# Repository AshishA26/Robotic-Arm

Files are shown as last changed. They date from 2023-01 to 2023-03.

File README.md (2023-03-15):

# Robotic-Arm
A robotic arm that mimics a user's arm gestures. It is purposed to help people with disabilities and meant for remote operations, and can also be used as a prototype in various other cases.

There are 2 parts to this project. The 1st part is the robotic arm itself, which has 5 DOF (5 servos / 5 "Degrees of Freedom") and uses an Arduino Nano, a Dedicated Servo Driver, and an NRF24L01 for recieving signals. The 2nd part is a gesture controller that straps onto the user's body. It has an Arduino Nano, an NRF24L01 module for transmitting data to the robotic arm, and 2 MPU6050's. The MPU6050s are velcroed onto the user's wrists, and then each direction of motion the user moves an arm in, causes a servo to move.

Programmed in `Arduino IDE`, models created in `Solidworks`, schematics created in `KiCad`.

Here is a very quick demo of the robotic arm being manipulated by the gesture controller that is strapped onto me. The full video is available [here](https://www.youtube.com/watch?v=RmKj0so72yQ). (Note: The white object in my hand is a switch to remotely power on/off the robotic arm.)
Link to youtube video (https://www.youtube.com/watch?v=RmKj0so72yQ)

Additionally, I made a demo video showing all the joints in the robotic arm moving one by one (using the gesture controller), which is available for viewing [here](https://www.youtube.com/watch?v=eJz9jL7be58).

A picture of the Robotic Arm:
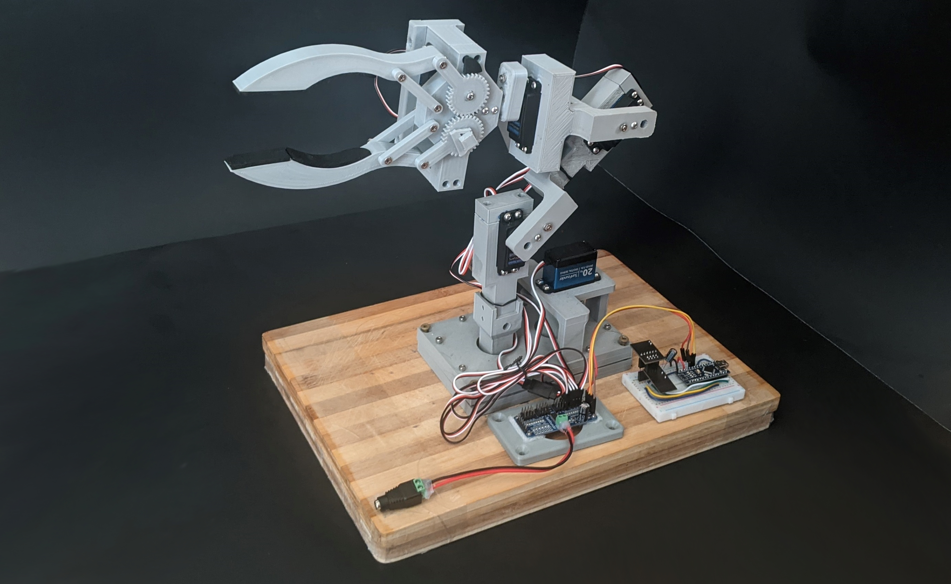
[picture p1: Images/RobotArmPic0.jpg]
RobotArmPic5


A picture of the Gesture Controller:
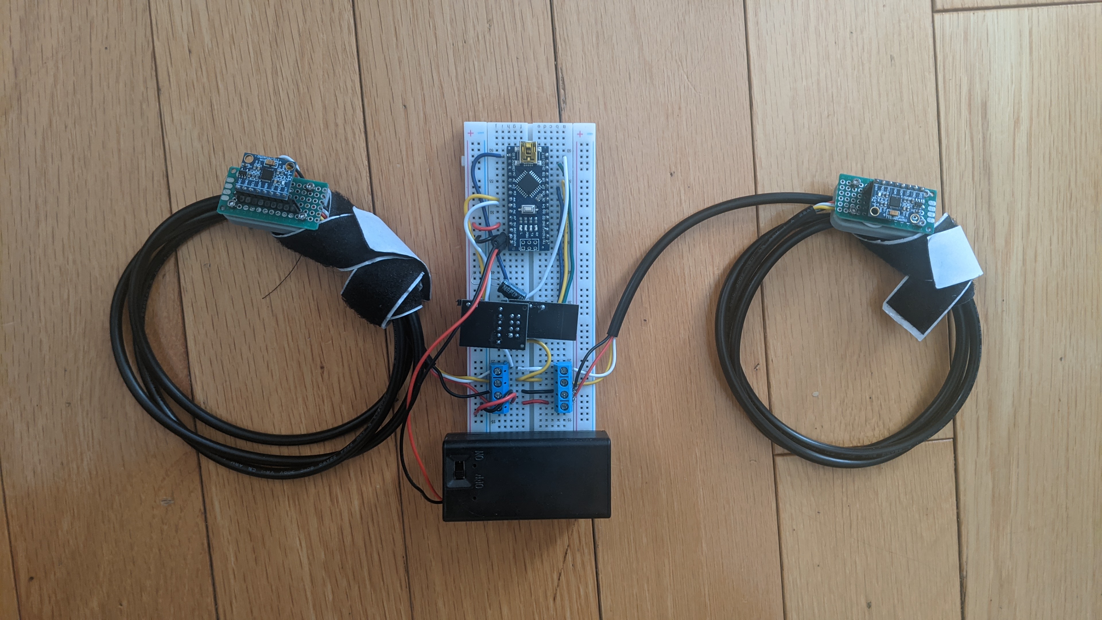
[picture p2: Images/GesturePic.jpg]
RobotArmPic6


## Schematics
RobotArmSchematic

## Demos
Some demos showing how certain mechanisms in the robotic arm work.

| Gear Movement Demo | Backside of Gears |
| :---: | :---: |
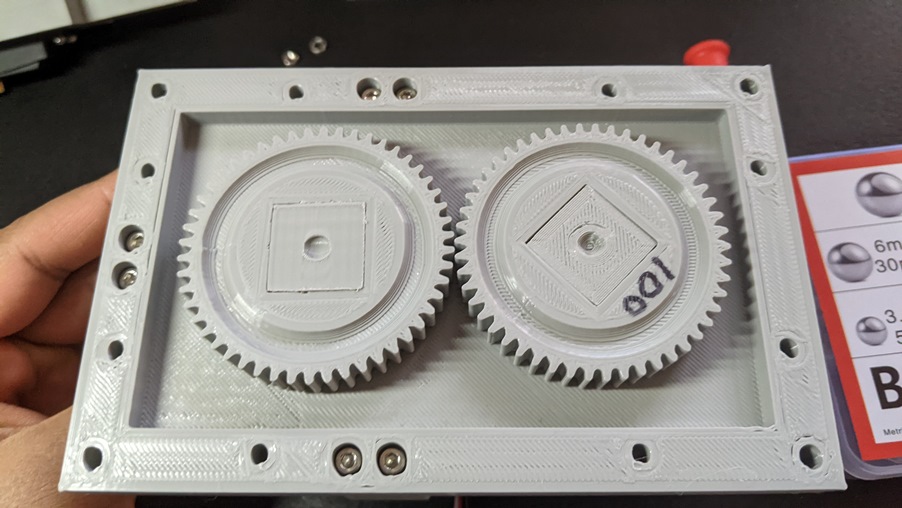
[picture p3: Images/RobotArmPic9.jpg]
BacksideOfGears
| GearDemo  |  |

<p align="center">
    <strong>Claw Demo</strong>
</p>

<p align="center">
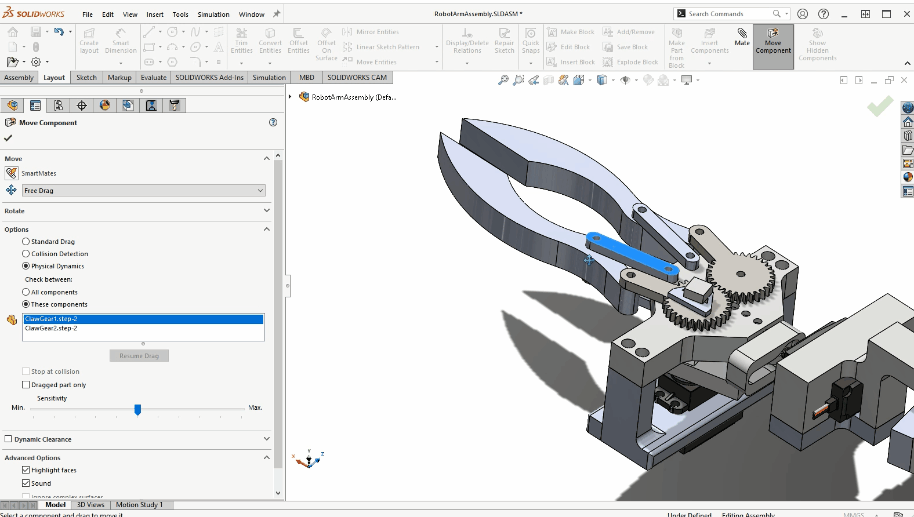
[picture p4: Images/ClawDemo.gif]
  
</p>

## Other Images
Rendered pictures of the 3D model I created using my own models designed for 3D printing combined with the servos from [GrabCAD](https://grabcad.com/library). Made in real-world scale and was designed using Solidworks:
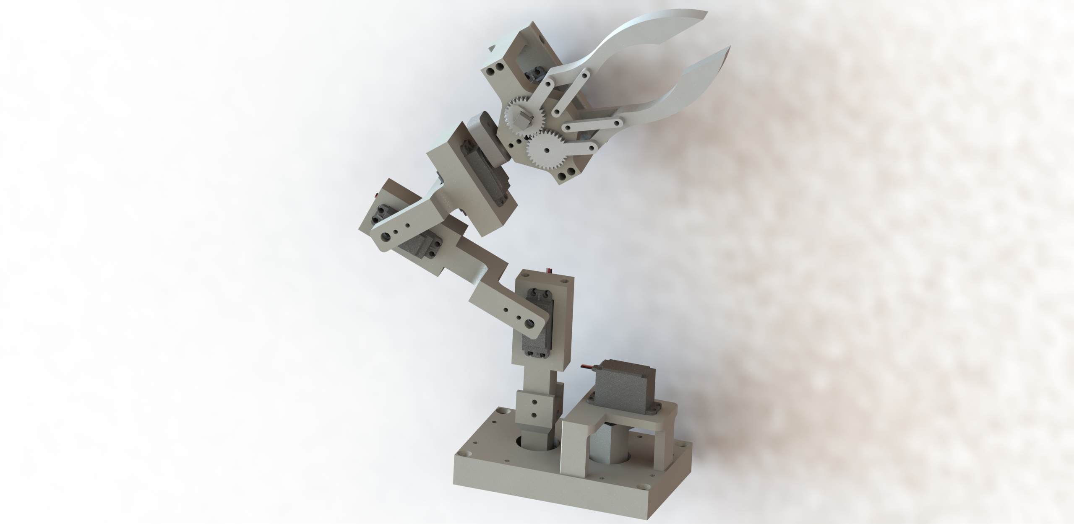
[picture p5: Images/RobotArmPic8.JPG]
RobotArmPic5


Render of gear mechanism underneath the lid.
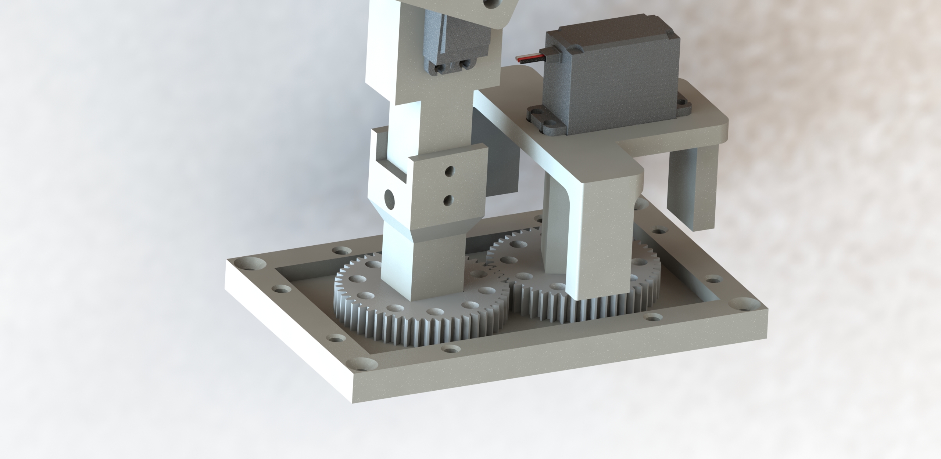
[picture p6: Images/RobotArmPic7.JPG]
RobotArmPic5


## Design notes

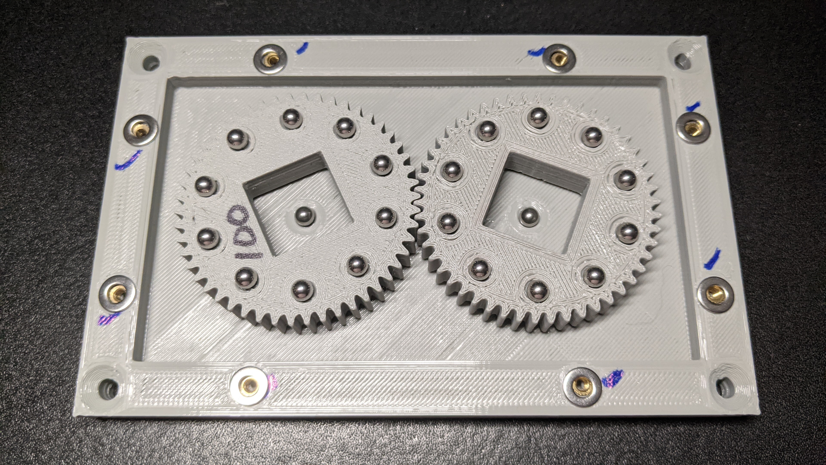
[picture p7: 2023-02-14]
Images/RobotArmPic10.jpg

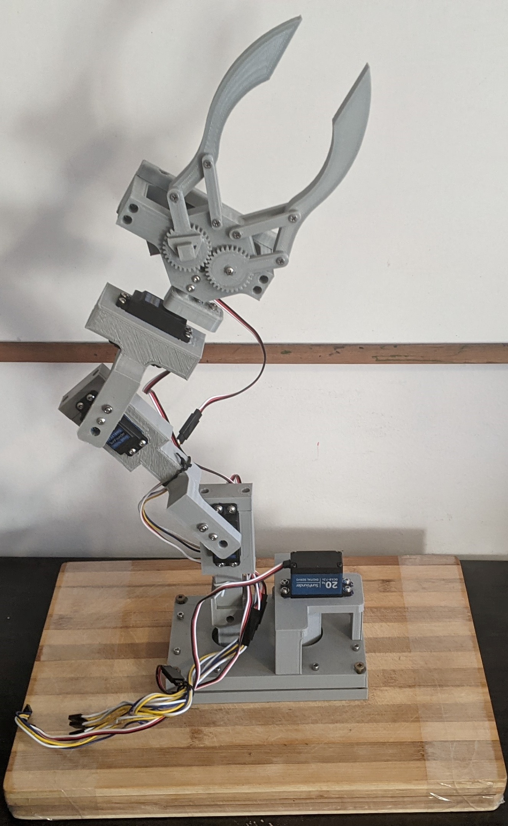
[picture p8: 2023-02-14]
Images/RobotArmPic6Cropped.jpg

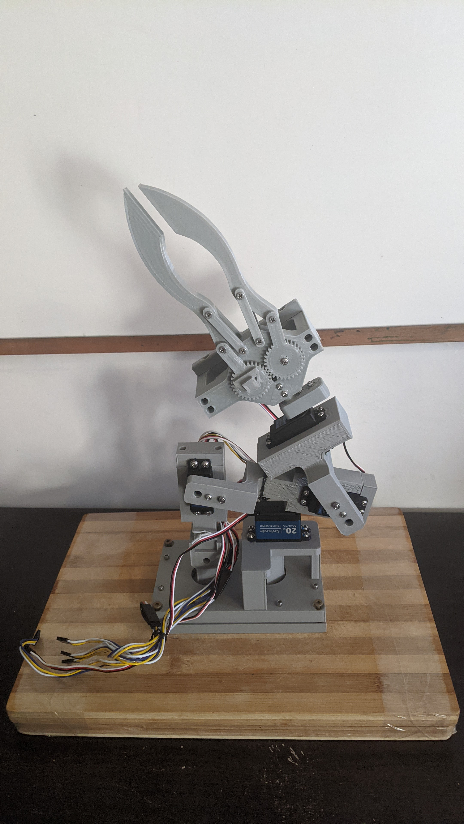
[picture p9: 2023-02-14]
Images/RobotArmPic2.jpg

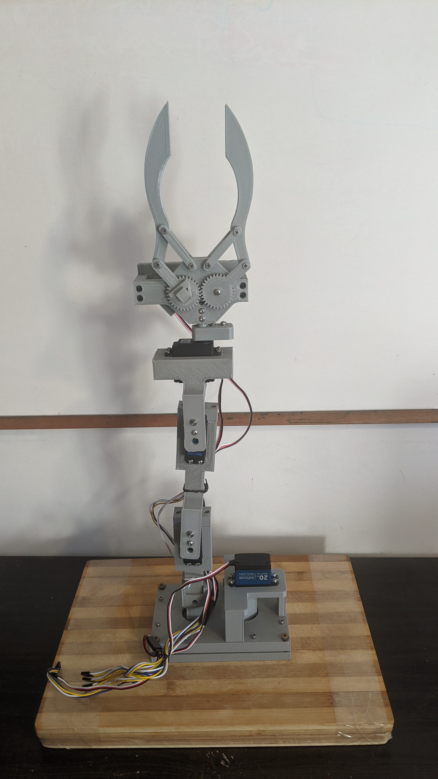
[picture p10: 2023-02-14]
Images/RobotArmPic1.jpg

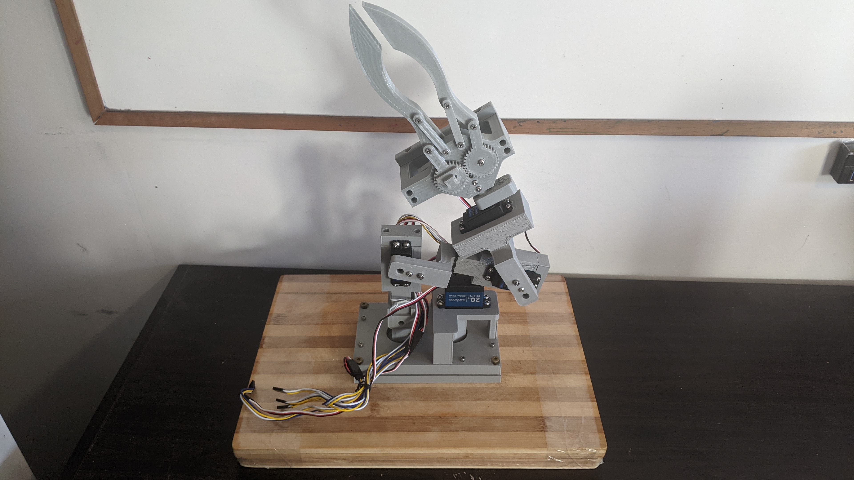
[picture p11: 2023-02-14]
Images/RobotArmPic4.jpg

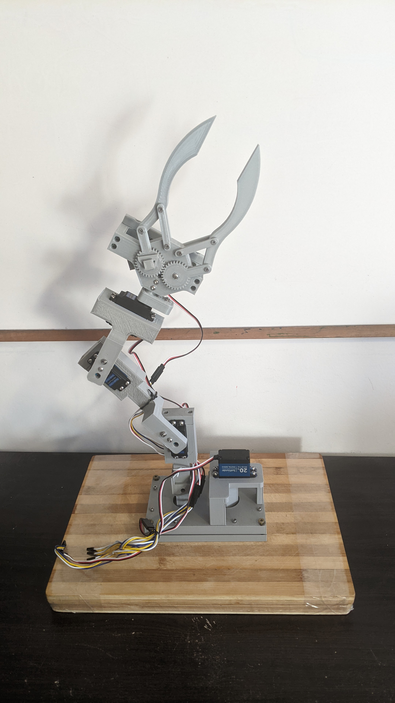
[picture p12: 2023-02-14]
Images/RobotArmPic3.jpg

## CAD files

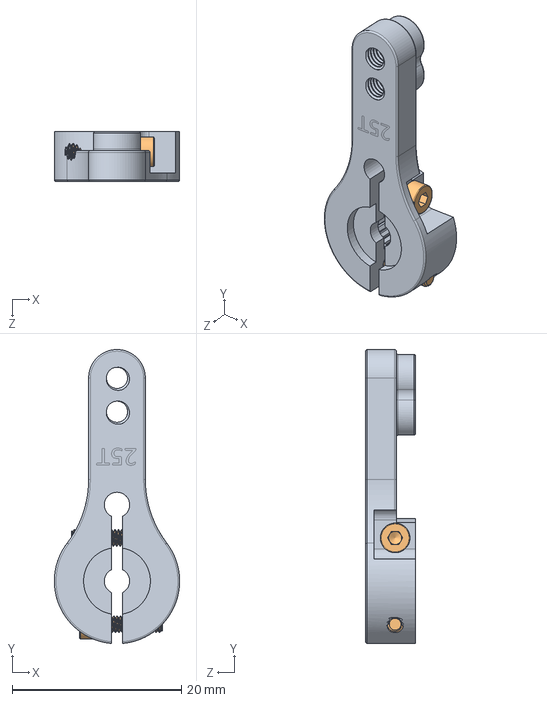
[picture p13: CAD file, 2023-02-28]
Models/Assembly/SERVO ARM HORN 25T ALUMINIUM/SERVO ARM HORN WITH FASTENERS.SLDASM
14.8 x 34.7 x 5.90 mm
SERVO ARM HORN 25T ALUMINIUM
M2 CAP HEAD SOCKET SCREW x 2

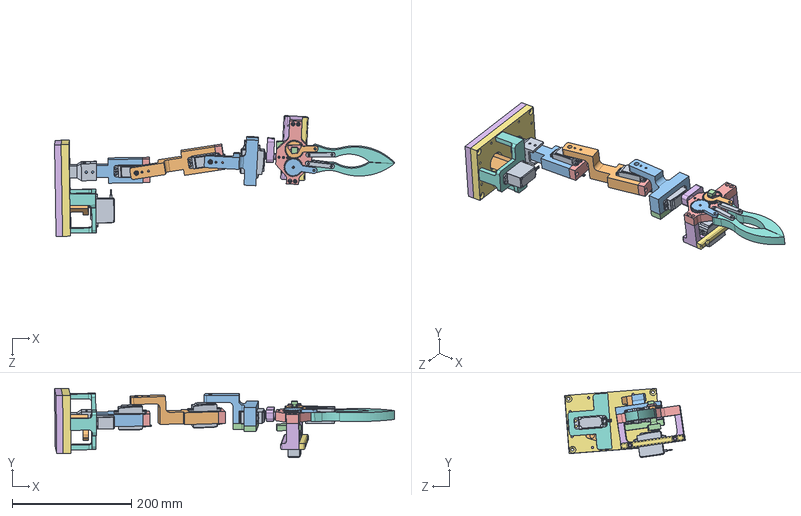
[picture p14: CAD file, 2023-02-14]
Models/Assembly/RobotArmAssembly.SLDASM
569.9 x 115.9 x 202.6 mm
sunfounder_20kgSLDPRT x 5
ServoArmMount
ArmPt1
ShaftGearSTEP x 2
ArmPt1Top x 2
BottomSideBaseCase
TopSideBaseCase
BaseServoStand
ArmExtension
ArmPt2
ArmPt3
ArmPt3Top
ArmPt4
ArmPt4ServoHolder
ArmPt4ServoHolderScrew
ClawGripper x 2
ClawJoint x 4
ClawGear1.step
ClawGear2.step
ServotoGear
ServotoGearClip
ArmPt4ServoArm

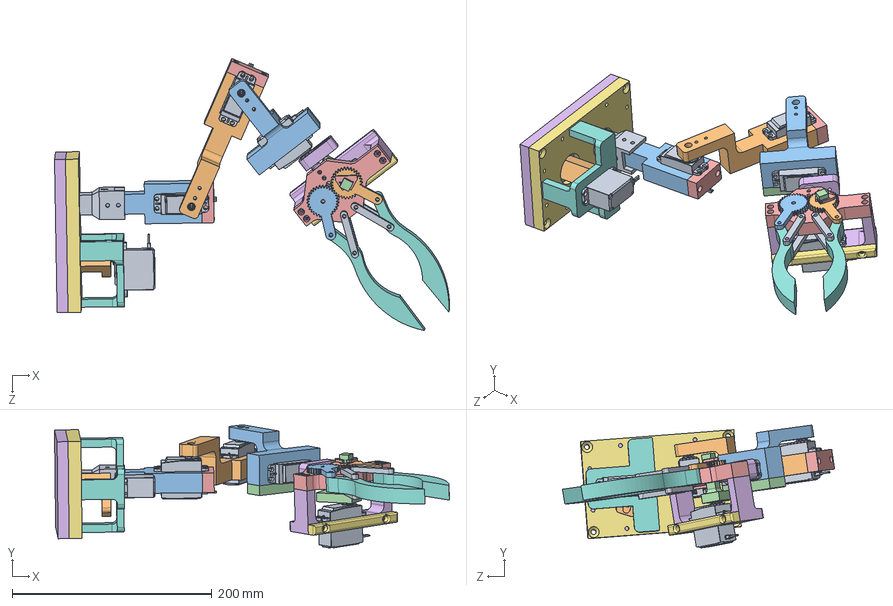
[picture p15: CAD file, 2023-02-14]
Models/Assembly/RobotArmAssemblyInBentShape.SLDASM
396.0 x 123.3 x 272.9 mm
sunfounder_20kgSLDPRT x 5
ServoArmMount
ArmPt1
ShaftGearSTEP x 2
ArmPt1Top x 2
BottomSideBaseCase
TopSideBaseCase
BaseServoStand
ArmExtension
ArmPt2
ArmPt3
ArmPt3Top
ArmPt4
ArmPt4ServoHolder
ArmPt4ServoHolderScrew
ClawGripper x 2
ClawJoint x 4
ClawGear1.step
ClawGear2.step
ServotoGear
ServotoGearClip
ArmPt4ServoArm

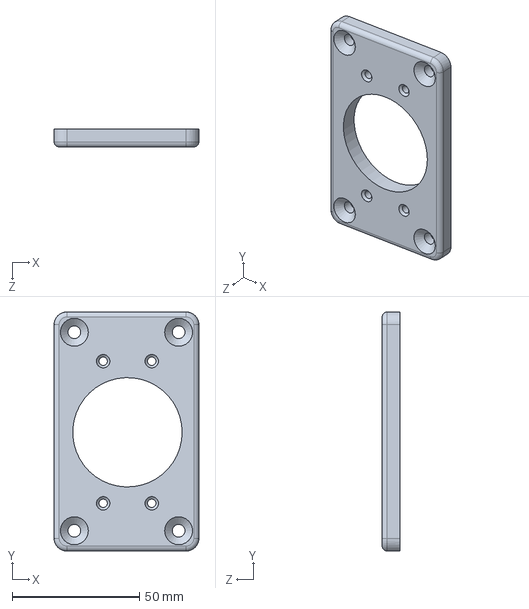
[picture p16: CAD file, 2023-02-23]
Models/Assembly/ServoDriverHolder.SLDPRT
57.0 x 94.0 x 7.00 mm

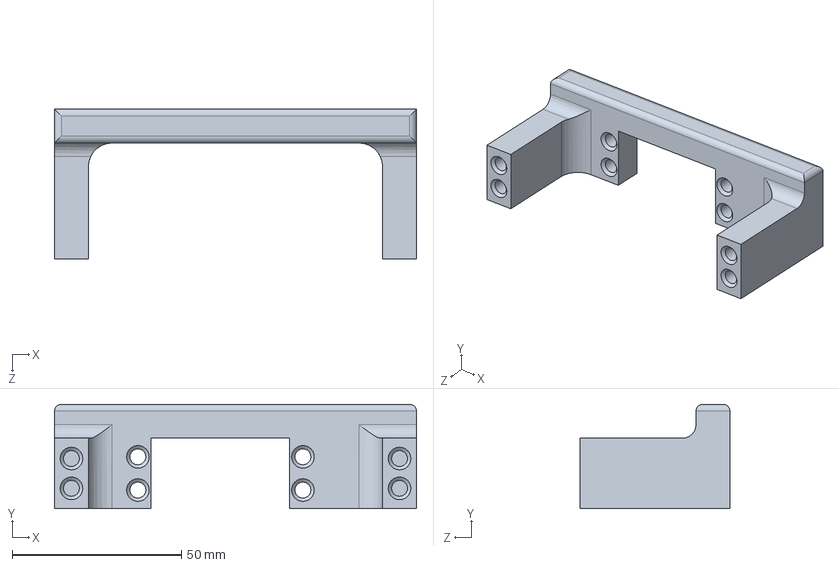
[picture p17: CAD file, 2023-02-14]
Models/Assembly/ArmPt4ServoHolder.SLDPRT
106.8 x 30.8 x 44.2 mm

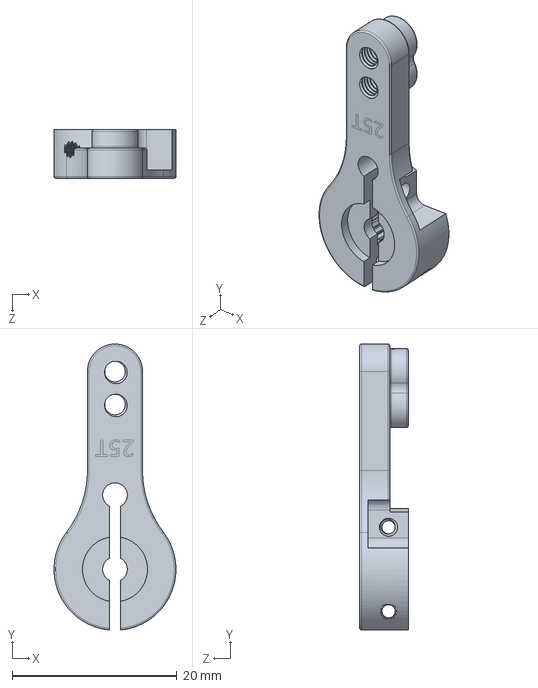
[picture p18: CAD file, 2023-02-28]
Models/Assembly/SERVO ARM HORN 25T ALUMINIUM/SERVO ARM HORN 25T ALUMINIUM.SLDPRT
14.8 x 34.7 x 5.90 mm

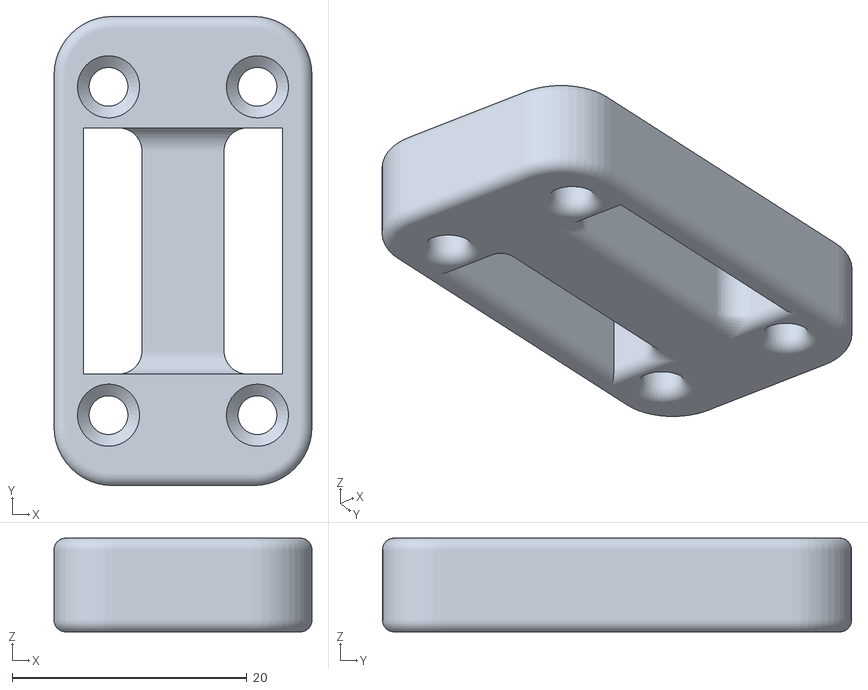
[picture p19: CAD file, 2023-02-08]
Models/STL/WristbandV1.STL
22.0 x 40.0 x 8.00

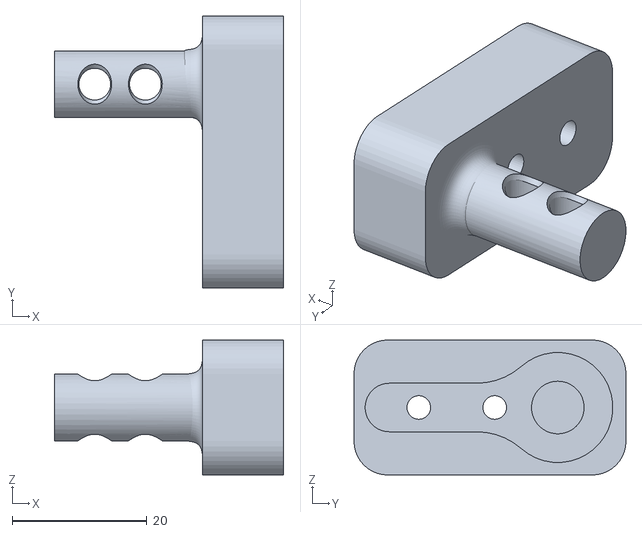
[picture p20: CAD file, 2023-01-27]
Models/STL/ArmPt4ServoArm.STL
34.0 x 40.3 x 20.0

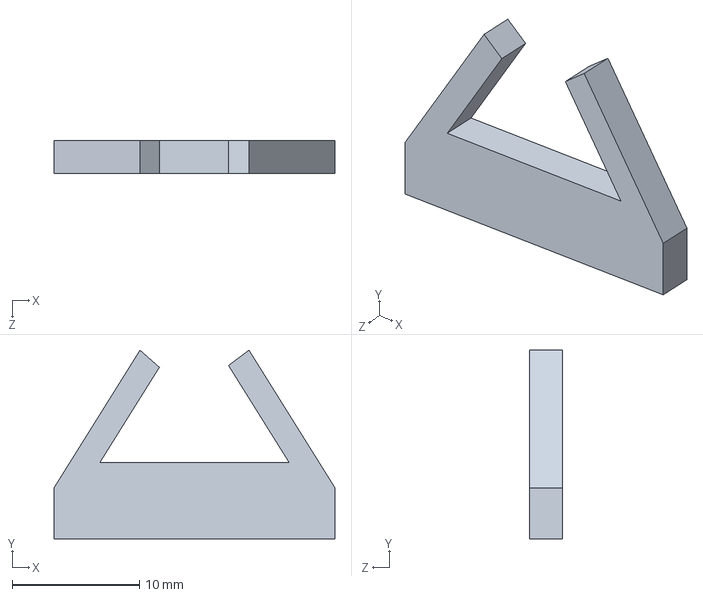
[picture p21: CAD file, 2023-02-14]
Models/Assembly/ServotoGearClip.SLDPRT
22.0 x 14.8 x 2.60 mm

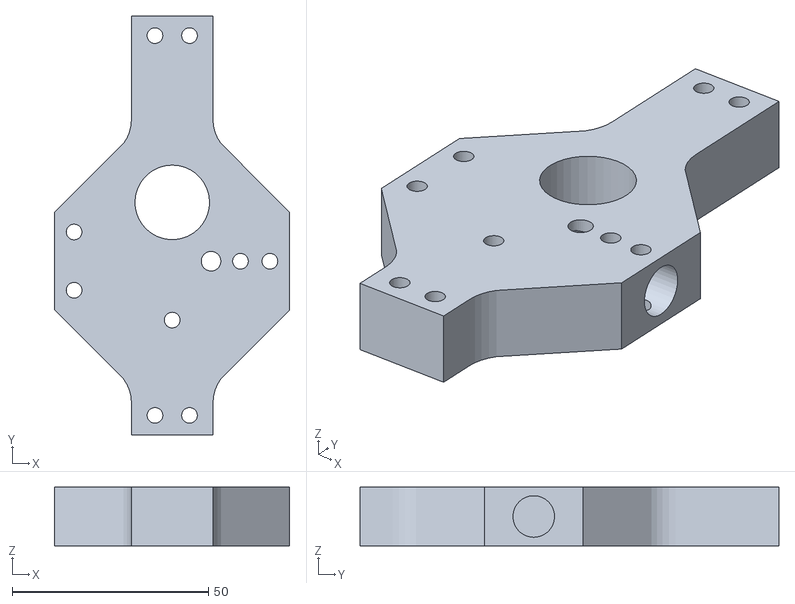
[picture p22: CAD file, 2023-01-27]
Models/STL/ArmPt4.STL
59.9 x 106.8 x 15.0

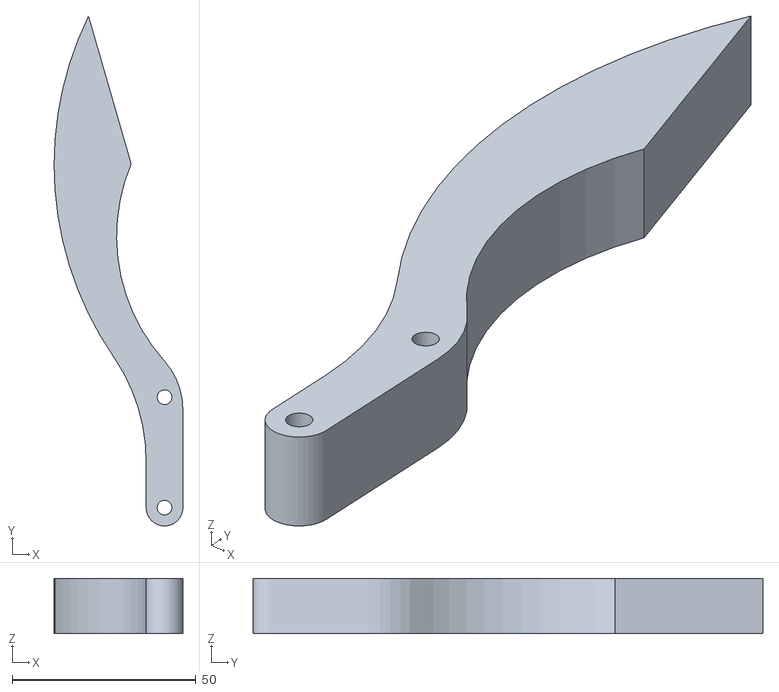
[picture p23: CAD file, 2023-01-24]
Models/STL/ClawGripper.STL
35.0 x 138.6 x 15.0

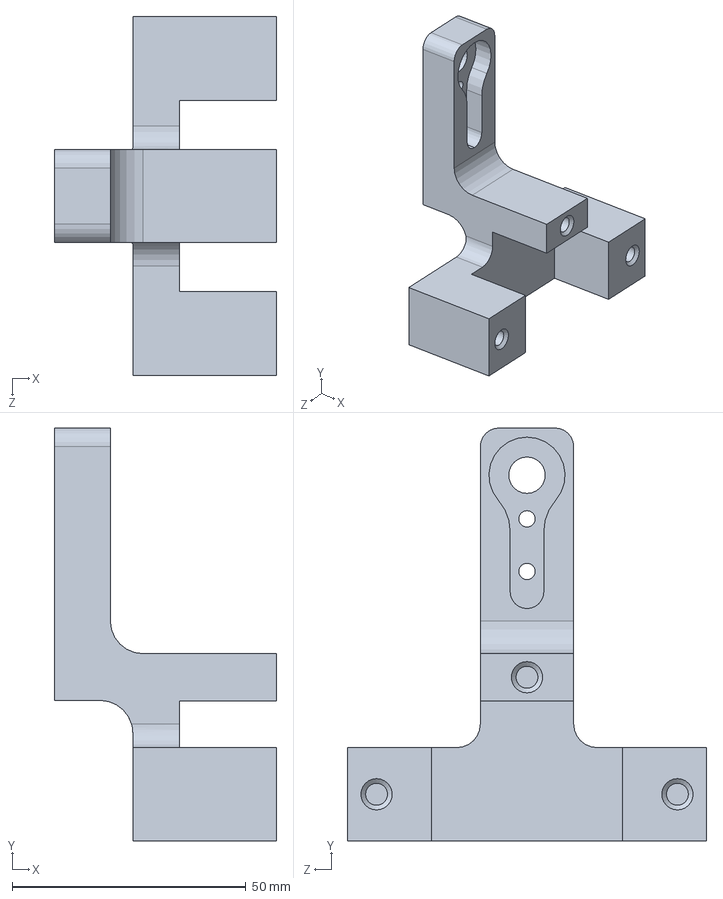
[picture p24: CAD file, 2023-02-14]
Models/Assembly/ArmPt3.SLDPRT
47.6 x 88.4 x 76.9 mm

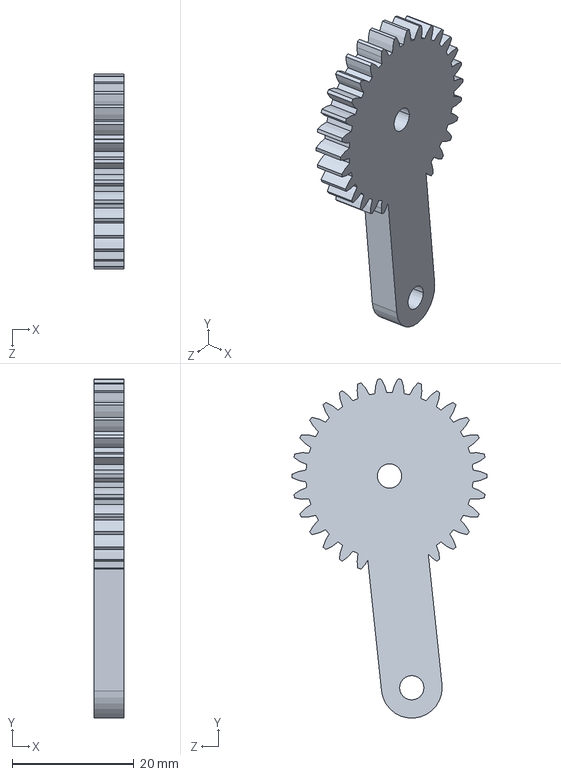
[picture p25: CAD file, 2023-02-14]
Models/Assembly/ClawGear2.step.SLDPRT
5.00 x 55.7 x 32.0 mm

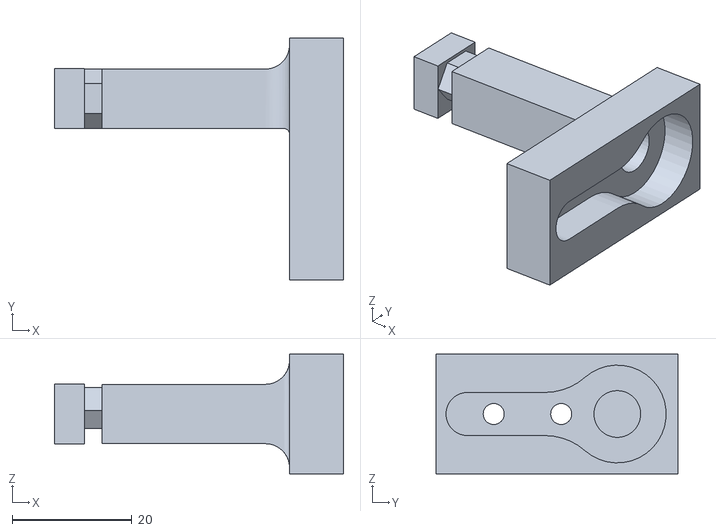
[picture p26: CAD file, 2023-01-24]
Models/STL/ServotoGear.STL
48.2 x 40.3 x 20.0

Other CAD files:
Models/STL/ServoDriverHolder.STL
Models/STL/ArmPt4ServoHolder.STL
Models/STL/ClawJoint.STL
Models/Assembly/ShaftGearSTEP.SLDPRT
Models/Assembly/ArmExtension.SLDPRT
Models/Assembly/ArmPt1.SLDPRT
Models/Assembly/ArmPt1Top.SLDPRT
Models/Assembly/ArmPt2.SLDPRT
Models/Assembly/ArmPt3Top.SLDPRT
Models/Assembly/ArmPt4.SLDPRT
Models/Assembly/ArmPt4ServoArm.SLDPRT
Models/Assembly/ArmPt4ServoHolderScrew.SLDPRT
Models/Assembly/BaseServoStand.SLDPRT
Models/Assembly/BottomSideBaseCase.SLDPRT
Models/Assembly/ClawGear1.SLDPRT
Models/Assembly/ClawGear1.step.SLDPRT
Models/Assembly/ClawGear2.SLDPRT
Models/Assembly/ClawGripper.SLDPRT
Models/Assembly/ClawJoint.SLDPRT
Models/Assembly/SERVO ARM HORN 25T ALUMINIUM/M2 CAP HEAD SOCKET SCREW.SLDPRT
Models/Assembly/SERVO ARM HORN 25T ALUMINIUM/M2 x 8 CAP HEAD SOCKET SCREW.IGS
Models/Assembly/SERVO ARM HORN 25T ALUMINIUM/M2 x 8 CAP HEAD SOCKET SCREW.STEP
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

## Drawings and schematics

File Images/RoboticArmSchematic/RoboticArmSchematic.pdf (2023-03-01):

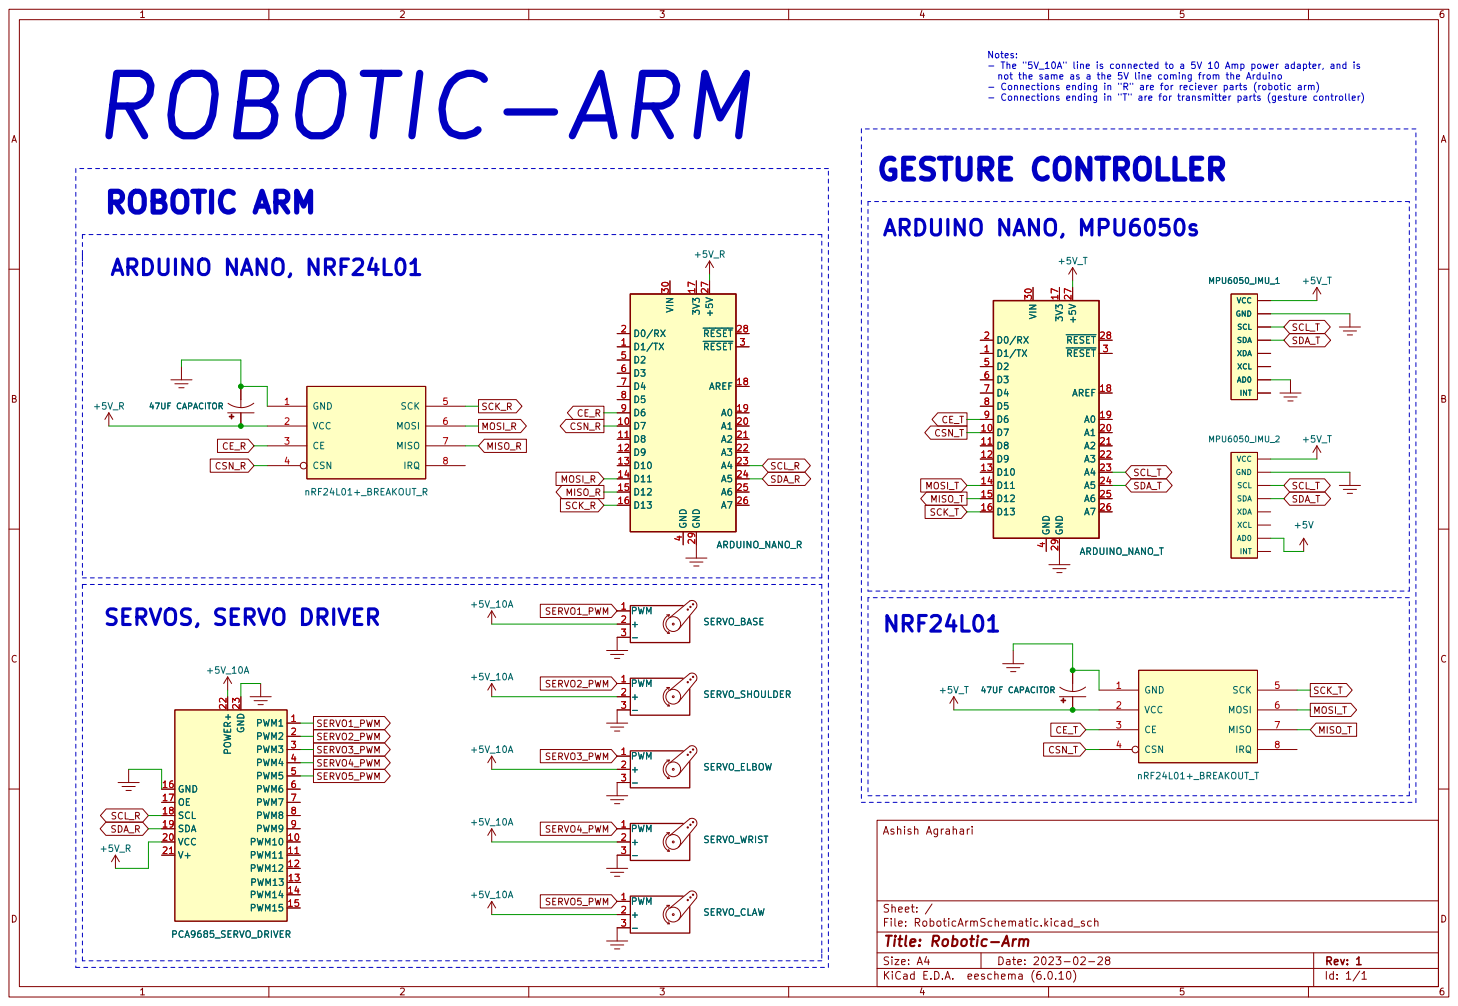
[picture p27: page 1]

Notes: - The "5V_10A" line is connected to a 5V 10 Amp power adapter, and is
~{RESET}28 GND 29

not the same as a the 5V line coming from the Arduino
- Connections ending in "R" are for reciever parts (robotic arm)
- Connections ending in "T" are for transmitter parts (gesture controller)

ROBOTIC ARM

File: RoboticArmSchematic.kicad_sch Sheet: / Ashish Agrahari +5V_10A

Id: 1/1 Title: Robotic-Arm

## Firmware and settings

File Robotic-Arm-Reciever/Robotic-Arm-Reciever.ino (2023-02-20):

// By Ashish Agrahari: https://github.com/AshishA26

#include <Wire.h>
#include <Adafruit_PWMServoDriver.h>
#include <SPI.h>
#include <nRF24L01.h>
#include <RF24.h>
RF24 radio(7, 8);   // nRF24L01 (CE, CSN), can be any digital pin on the arduino

// called this way, it uses the default address 0x40
// pwm is adafruits library meant to mimic things like servo.writeMicroseconds in order for them to use it on the dedicated servo driver
Adafruit_PWMServoDriver pwm = Adafruit_PWMServoDriver();

#define SERVOMIN  600 // This is the rounded 'minimum' microsecond length, in this case the servo can have a minimum of 600 (600-2400 for 270 degrees rotation)
#define SERVOMAX  2400 // This is the rounded 'maximum' microsecond length, in this case the servo can have a maximum of 2400
#define SERVO_FREQ 50 // Analog servos run at ~50 Hz updates

// our servo # counter
uint8_t servo[] = {0, 1, 2, 3, 4, 5};
float servoMap[] = {0, 0, 0, 0, 0, 0};
float servoPos[] = {127, 127, 127, 127, 127, 127};
float servoMapR = 0;

#define MPUBeginHigh  137
#define MPUBeginLow  117
#define MPUCheckHigh  140
#define MPUCheckLow  114
#define delayTime  20

const byte address[6] = "00001";
unsigned long lastReceiveTime = 0;
unsigned long currentTime = 0;
// Max size of this struct is 32 bytes - NRF24L01 buffer limit
struct Data_Package {
  byte MPU0_y;
  byte MPU0_p;
  byte MPU0_r;
  byte MPU1_y;
  byte MPU1_p;
  byte MPU1_r;
};
Data_Package data; //Create a variable with the above structure

void resetData() {
  // Reset the values when there is no radio connection - Set initial default values
  // 127 because byte value is 0-255, so 127 is middle
  data.MPU0_y = 127;
  data.MPU0_p = 127;
  data.MPU0_r = 127;
  data.MPU1_y = 127;
  data.MPU1_p = 127;
  data.MPU1_r = 127;
  for (byte b = 0; b < 6; b++) {
    servoMapR = map(127, 255, 0, SERVOMIN, SERVOMAX);
    pwm.writeMicroseconds(servo[b], servoMapR);
    servoPos[b] = 127;
  }
}

void setup() {
  Serial.begin(115200);
  Serial.println("Beginning...");

  pwm.begin();
  pwm.setOscillatorFrequency(27000000);
  pwm.setPWMFreq(SERVO_FREQ);  // Analog servos run at ~50 Hz updates

  radio.begin();
  radio.openReadingPipe(0, address);
  radio.setAutoAck(false);
  radio.setDataRate(RF24_250KBPS);
  radio.setPALevel(RF24_PA_MIN); // It was originally LOW
  radio.startListening(); //  Set the module as receiver
  resetData();
}

/*
 * Function to check if other axis' are centered (or close to their center positions) as 2 axis' should not be moving at the same time. 
 * 2 axis motion at the same time has been stopped because, for example, if the MPU had a yaw of 0 and a roll of 0, and then the yaw 
 * was moved to say 65, then the roll would for no reason change to something like 180. This is most likely due to the programmed 
 * mathematics in the MPU itself. So this is just to prevent any weird motion.
*/
int checkOtherAxis(int axisNumber) {
  if (axisNumber == 0) {
    if (data.MPU0_p > MPUCheckHigh or data.MPU0_p < MPUCheckLow or data.MPU0_r > MPUCheckHigh or data.MPU0_r < MPUCheckLow) {
      return 0;
    }
    else {
      return 1;
    }
  }
  else if (axisNumber == 4) {
    if (data.MPU0_y > MPUCheckHigh or data.MPU0_y < MPUCheckLow or data.MPU0_r > MPUCheckHigh or data.MPU0_r < MPUCheckLow) {
      return 0;
    }
    else {
      return 1;
    }
  }
  else if (axisNumber == 3) {
    if (data.MPU1_r > MPUCheckHigh or data.MPU1_r < MPUCheckLow or data.MPU1_y > MPUCheckHigh or data.MPU1_y < MPUCheckLow) {
      return 0;
    }
    else {
      return 1;
    }
  }
  else if (axisNumber == 2) {
    if (data.MPU1_p > MPUCheckHigh or data.MPU1_p < MPUCheckLow or data.MPU1_y > MPUCheckHigh or data.MPU1_y < MPUCheckLow) {
      return 0;
    }
    else {
      return 1;
    }
  }
  else if (axisNumber == 1) {
    if (data.MPU0_y > MPUCheckHigh or data.MPU0_y < MPUCheckLow or data.MPU0_p > MPUCheckHigh or data.MPU0_p < MPUCheckLow) {
      return 0;
    }
    else {
      return 1;
    }
  }
}

void loop() {

  // Check whether there is data to be received
  if (radio.available()) {
    radio.read(&data, sizeof(Data_Package)); // Read the whole data and store it into the 'data' structure
    lastReceiveTime = millis(); // At this moment we have received the data
    //    Serial.println("Available");
    Serial.print("MPU0_y: ");
    Serial.print(data.MPU0_y);
    Serial.print("; MPU0_p: ");
    Serial.print(data.MPU0_p);
    Serial.print("; MPU0_r: ");
    Serial.print(data.MPU0_r);
    Serial.print("; MPU1_y: ");
    Serial.print(data.MPU1_y);
    Serial.print("; MPU1_p: ");
    Serial.print(data.MPU1_p);
    Serial.print("; MPU1_r: ");
    Serial.print(data.MPU1_r);
    Serial.println("");

    // Note: Servos are numbered from bottom to top. Also, there is only 5 servos, so I have decided to not use the axis MPU1_y.
    // Below if statements are to limit servo motion to prevent parts from hitting each other. Also checks whether MPU has been tilted above or below a certain number, and checks if other axises are (almost) centered.
    
    // Base
    if (data.MPU0_y > MPUBeginHigh and servoPos[0] < 255 and checkOtherAxis(0) == 1) {
      servoPos[0] = servoPos[0] + 1;
      servoMap[0] = map(servoPos[0], 255, 0, SERVOMIN, SERVOMAX);
      delay(delayTime);
    }
    else if (data.MPU0_y < MPUBeginLow and servoPos[0] > 0 and checkOtherAxis(0) == 1) {
      servoPos[0] = servoPos[0] - 1;
      servoMap[0] = map(servoPos[0], 255, 0, SERVOMIN, SERVOMAX);
      delay(delayTime);
    }

    // Shoulder
    else if (data.MPU0_r > MPUBeginHigh and servoPos[1] < 205 and checkOtherAxis(1) == 1) {
      servoPos[1] = servoPos[1] + 1;
      servoMap[1] = map(servoPos[1], 255, 0, SERVOMIN, SERVOMAX);
      delay(delayTime);
    }
    else if (data.MPU0_r < MPUBeginLow and servoPos[1] > 50 and checkOtherAxis(1) == 1) {
      servoPos[1] = servoPos[1] - 1;
      servoMap[1] = map(servoPos[1], 255, 0, SERVOMIN, SERVOMAX);
      delay(delayTime);
    }

    // Elbow
    else if (data.MPU1_r > MPUBeginHigh and servoPos[2] < 205 and checkOtherAxis(2) == 1) {
      servoPos[2] = servoPos[2] + 1;
      servoMap[2] = map(servoPos[2], 255, 0, SERVOMIN, SERVOMAX);
      delay(delayTime);
    }
    else if (data.MPU1_r < MPUBeginLow and servoPos[2] > 50 and checkOtherAxis(2) == 1) {
      servoPos[2] = servoPos[2] - 1;
      servoMap[2] = map(servoPos[2], 255, 0, SERVOMIN, SERVOMAX);
      delay(delayTime);
    }

    // Wrist
    else if (data.MPU1_p > MPUBeginHigh and servoPos[3] < 255 and checkOtherAxis(3) == 1) {
      servoPos[3] = servoPos[3] + 1;
      servoMap[3] = map(servoPos[3], 255, 0, SERVOMIN, SERVOMAX);
      delay(delayTime);
    }
    else if (data.MPU1_p < MPUBeginLow and servoPos[3] > 0 and checkOtherAxis(3) == 1) {
      servoPos[3] = servoPos[3] - 1;
      servoMap[3] = map(servoPos[3], 255, 0, SERVOMIN, SERVOMAX);
      delay(delayTime);
    }

    // Claw
    else if (data.MPU0_p > MPUBeginHigh and servoPos[4] < 171 and checkOtherAxis(4) == 1) {
      servoPos[4] = servoPos[4] + 1;
      servoMap[4] = map(servoPos[4], 255, 0, SERVOMIN, SERVOMAX);
      delay(delayTime);
    }
    else if (data.MPU0_p < MPUBeginLow and servoPos[4] > 111 and checkOtherAxis(4) == 1) {
      servoPos[4] = servoPos[4] - 1;
      servoMap[4] = map(servoPos[4], 255, 0, SERVOMIN, SERVOMAX);
      delay(delayTime);
    }

    // Writes values to each servo
    for (byte b = 0; b < 6; b++) {
      pwm.writeMicroseconds(servo[b], servoMap[b]);
    }
  }

  // Check whether we keep receving data, or we have a connection between the two modules
  currentTime = millis();
  if ( currentTime - lastReceiveTime > 1000 ) { // If current time is more then 1 second since we have recived the last data, that means we have lost connection
    //resetData(); // This is commented out because if the nRF does disconnect, we don't want the arm to fling into its default position, we want to to stay in its previous position.
    Serial.println("nRF DISCONNECTED");
  }
}

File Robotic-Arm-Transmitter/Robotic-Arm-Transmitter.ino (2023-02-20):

// By Ashish Agrahari: https://github.com/AshishA26

// I2Cdev and MPU6050 must be installed as libraries, or else the .cpp/.h files
// for both classes must be in the include path of your project
#include "I2Cdev.h"
#include "MPU6050_6Axis_MotionApps20.h"
#include <SPI.h>
#include <nRF24L01.h>
#include <RF24.h>
#include <Wire.h>

MPU6050 mpu[] = {0x68, 0x69};// AD0 low = 0x68, AD0 high = 0x69

#define INTERRUPT_PIN 2  // use pin 2 on Arduino Uno & most boards
#define LED_PIN 13 // (Arduino is 13, Teensy is 11, Teensy++ is 6)
bool blinkState = false;

// MPU control/status vars
bool dmpReady = false;  // set true if DMP init was successful
uint8_t mpuIntStatus[] = {0, 0};   // holds actual interrupt status byte from MPU
uint8_t devStatus;      // return status after each device operation (0 = success, !0 = error)
uint16_t packetSize[] = {0, 0};    // expected DMP packet size (default is 42 bytes)
uint16_t fifoCount;     // count of all bytes currently in FIFO
uint8_t fifoBuffer[64]; // FIFO storage buffer

// orientation/motion vars
Quaternion q;           // [w, x, y, z]         quaternion container
VectorInt16 aa;         // [x, y, z]            accel sensor measurements
VectorInt16 aaReal;     // [x, y, z]            gravity-free accel sensor measurements
VectorInt16 aaWorld;    // [x, y, z]            world-frame accel sensor measurements
VectorFloat gravity;    // [x, y, z]            gravity vector
float ypr[3];           // [yaw, pitch, roll]   yaw/pitch/roll container and gravity vector

float MPU_y[] = {0, 0};
float MPU_p[] = {0, 0};
float MPU_r[] = {0, 0};

RF24 radio(7, 8);   // nRF24L01 (CE, CSN)
const byte address[6] = "00001"; // Address

// Max size of this struct is 32 bytes - NRF24L01 buffer limit
struct Data_Package {
  byte MPU0_y;
  byte MPU0_p;
  byte MPU0_r;
  byte MPU1_y;
  byte MPU1_p;
  byte MPU1_r;
};
Data_Package data; //Create a variable with the above structure

volatile bool mpuInterrupt = false;     // indicates whether MPU interrupt pin has gone high
void dmpDataReady() {
  mpuInterrupt = true;
}

void setup() {
  // join I2C bus (I2Cdev library doesn't do this automatically)
#if I2CDEV_IMPLEMENTATION == I2CDEV_ARDUINO_WIRE
  Wire.begin();
  Wire.setClock(400000); // 400kHz I2C clock. Comment this line if having compilation difficulties
  Wire.setWireTimeout(3000, true); // VERY IMPORTANT!!! THIS FIXES THE I2C BUS FROM HANGING
#elif I2CDEV_IMPLEMENTATION == I2CDEV_BUILTIN_FASTWIRE
  Fastwire::setup(400, true);
#endif

  Serial.begin(115200);
  while (!Serial);

  // initialize device
  Serial.println(F("Initializing I2C devices..."));
  for (byte b = 0; b < 2; b++)
  {
    mpu[b].initialize();
    pinMode(INTERRUPT_PIN, INPUT);

    Serial.print("MPU#");
    Serial.print(b);
    Serial.println(":");
    // verify connection
    Serial.println(F("Testing device connections..."));
    Serial.println(mpu[b].testConnection() ? F("MPU6050 connection successful") : F("MPU6050 connection failed"));

    // load and configure the DMP
    Serial.println(F("Initializing DMP..."));
    devStatus = mpu[b].dmpInitialize();

    // supply your own gyro offsets here, scaled for min sensitivity
    mpu[b].setXGyroOffset(220);
    mpu[b].setYGyroOffset(76);
    mpu[b].setZGyroOffset(-85);
    mpu[b].setZAccelOffset(1788); // 1688 factory default for my test chip

    // make sure it worked (returns 0 if so)
    if (devStatus == 0) {
      // Calibration Time: generate offsets and calibrate our MPU6050
      mpu[b].CalibrateAccel(6);
      mpu[b].CalibrateGyro(6);
      mpu[b].PrintActiveOffsets();
      // turn on the DMP, now that it's ready
      Serial.println(F("Enabling DMP ..."));
      mpu[b].setDMPEnabled(true);

      // enable Arduino interrupt detection
      Serial.print(F("Enabling interrupt detection (Arduino external interrupt "));
      Serial.print(digitalPinToInterrupt(INTERRUPT_PIN));
      Serial.println(F(")..."));
      attachInterrupt(digitalPinToInterrupt(INTERRUPT_PIN), dmpDataReady, RISING);
      mpuIntStatus[b] = mpu[b].getIntStatus();

      // set our DMP Ready flag so the main loop() function knows it's okay to use it
      Serial.println(F("DMP ready! Waiting for first interrupt..."));
      dmpReady = true;

      // get expected DMP packet size for later comparison
      packetSize[b] = mpu[b].dmpGetFIFOPacketSize();
    } else {
      // ERROR!
      // 1 = initial memory load failed
      // 2 = DMP configuration updates failed
      // (if it's going to break, usually the code will be 1)
      Serial.print(F("DMP Initialization failed (code "));
      Serial.print(devStatus);
      Serial.println(F(")"));
    }
  }
  // configure LED for output
  pinMode(LED_PIN, OUTPUT);

  // Define the radio communication
  radio.begin();
  radio.openWritingPipe(address);
  radio.setAutoAck(false);
  radio.setDataRate(RF24_250KBPS);
  radio.setPALevel(RF24_PA_MIN); // It was originally LOW

  data.MPU0_y = 0;
  data.MPU0_p = 0;
  data.MPU0_r = 0;
  data.MPU1_y = 0;
  data.MPU1_p = 0;
  data.MPU1_r = 0;
}

void loop() {
  // if programming failed, don't try to do anything
  if (!dmpReady) return;
  for (byte b = 0; b < 2; b++) {
    // read a packet from FIFO
    if (mpu[b].dmpGetCurrentFIFOPacket(fifoBuffer)) { // Get the Latest packet
      // display Euler angles in degrees
      mpu[b].dmpGetQuaternion(&q, fifoBuffer);
      mpu[b].dmpGetGravity(&gravity, &q);
      mpu[b].dmpGetYawPitchRoll(ypr, &q, &gravity);
      //      Serial.print("mpu#");
      //      Serial.print(b);
      //      Serial.print("\t");
      //      Serial.print(ypr[0] * 180 / M_PI);
      //      Serial.print("\t");
      //      Serial.print(ypr[1] * 180 / M_PI);
      //      Serial.print("\t");
      //      Serial.println(ypr[2] * 180 / M_PI);

      MPU_y[b] = ypr[0] * 180 / M_PI;
      MPU_p[b] = ypr[1] * 180 / M_PI;
      MPU_r[b] = ypr[2] * 180 / M_PI;
    }
    // blink LED to indicate activity
    blinkState = !blinkState;
    digitalWrite(LED_PIN, blinkState);
  }

  //Map the data from MPU to 0-255 range and then round it to be able to send in bytes, and set it to the data variables being sent
  data.MPU0_y = round(map(MPU_y[0], -180, 180, 0, 255));
  data.MPU0_p = round(map(MPU_p[0], -180, 180, 0, 255));
  data.MPU0_r = round(map(MPU_r[0], -180, 180, 0, 255));
  data.MPU1_y = round(map(MPU_y[1], -180, 180, 0, 255));
  data.MPU1_p = round(map(MPU_p[1], -180, 180, 0, 255));
  data.MPU1_r = round(map(MPU_r[1], -180, 180, 0, 255));

  Serial.print("MPU0_y: ");
  Serial.print(data.MPU0_y);
  Serial.print("; MPU0_p: ");
  Serial.print(data.MPU0_p);
  Serial.print("; MPU0_r: ");
  Serial.print(data.MPU0_r);
  Serial.print("; MPU1_y: ");
  Serial.print(data.MPU1_y);
  Serial.print("; MPU1_p: ");
  Serial.print(data.MPU1_p);
  Serial.print("; MPU1_r: ");
  Serial.print(data.MPU1_r);
  Serial.println("");

  // Send the whole data from the structure to the receiver
  radio.write(&data, sizeof(Data_Package));
}

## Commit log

2022-10-30 Uploading models
    [ArmExtension.SLDPRT, ArmExtension.STL, ArmPt1.SLDPRT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]
2022-11-28 Fixed NRF modules, updated code, fixed angles
    [Robotic-Arm-Reciever.ino, Robotic-Arm-Transmitter.ino]
2023-01-04 Added next piece of arm
    [ArmExtension.SLDPRT, ArmPt1.SLDPRT, ArmPt1Top.SLDPRT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]
2023-01-05 Created next arm part
    [ArmPt3.SLDPRT, ArmPt3.STL, ArmPt3Top.SLDPRT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]
2023-01-22 Working on claw
    [ArmPt4.SLDPRT, ArmPt4ServoHolder.SLDPRT, ArmPt4ServoHolderScrew.SLDPRT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]
2023-01-22 Almost done claw
    [ArmPt4.SLDPRT, ClawGear1.SLDPRT, ClawGear1.step.SLDPRT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]
2023-01-23 done modeling cla
    [ArmPt4.SLDPRT, ArmPt4ServoHolder.SLDPRT, ArmPt4ServoHolderScrew.SLDPRT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]
2023-01-24 Updated some models
    [ArmPt4ServoHolder.SLDPRT, ArmPt4ServoHolder.STL, ArmPt4ServoHolderScrew.STL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]
2023-01-27 Finished modelling
    [ArmPt4.SLDPRT, ArmPt4.STL, ArmPt4ServoArm.SLDPRT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]
2023-02-04 Working on mapping servos to MPU
2023-02-04 Workinng on servo controls
2023-02-08 Created wristband model for MPU
    [WristbandV1.SLDPRT, WristbandV1.STL]
2023-02-08 Removed reflections from scene
    [RobotArmAssembly.SLDASM]
2023-02-14 Fixed colors on parts, added images to repo
    [ArmExtension.SLDPRT, ArmPt1.SLDPRT, ArmPt1Top.SLDPRT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]
2023-02-19 Fixed servo limits, need to fix servo mapping and MPU drift
    [Robotic-Arm-Reciever.ino, Robotic-Arm-Transmitter.ino]
2023-02-20 Working on mapping servos
2023-02-23 Added servo-driver holder model
    [ServoDriverHolder.SLDPRT, ServoDriverHolder.STL]
2023-02-28 Working on schematic
    [M2 CAP HEAD SOCKET SCREW.SLDPRT, M2 x 8 CAP HEAD SOCKET SCREW.IGS, M2 x 8 CAP HEAD SOCKET SCREW.STEP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]
2023-03-01 Created schematics
    [RoboticArmSchematic.kicad_pcb, RoboticArmSchematic.kicad_sch]
2023-03-15 Added videos/gif of robotic arm
